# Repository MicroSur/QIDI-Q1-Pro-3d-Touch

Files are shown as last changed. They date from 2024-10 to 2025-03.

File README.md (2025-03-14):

# QIDI-Q1-Pro-3d-Touch

Переделка QIDI Q1 Pro с индуктивного датчика стола на 3д-тач для прошивки OpenQ1

Что плохо:
- все это справедливо для кастомной прошивки OpenQ1 ( https://github.com/frap129/OpenQ1 ), для стоковой прошивки Не подходит.
- нужно отрезать уши крепления у тача.
- подрезать уголок передней крышки головы (фото), чтобы снималась как раньше.
- Переписать в printer.cfg все координаты, где использовался индуктивный датчик на новые (примеры внизу)
- иметь кримпер для фиксации проводов в разъемы
- Это должно напугать и остановить, если нет то дальше...

Что надо:
- 3д-тач. Я брал у треугольников. https://aliexpress.ru/item/32949450525.html?sku_id=12000025395041340
  Можно любой, лишь бы влез в крепление и вы знаете распиновку.
  Распиновка используемого тача по цветам на фото.
- Распечатать крепление (stl), Тач должен крепко садиться в гнездо. У меня из ABS. Ориентацию на столе поменяйте, как вам удобно.
  Крепление в исходнике не мое, отредактировал для QIDI Q1 Pro добавив 10мм проставку. Исходник для qidi max3: https://www.printables.com/model/590047-qidi-x-max-3-x-plus-3-bl-touch-holder
- Распиновка (фото), используются pазъемы на плате головы J7 ( +5, Gnd, IO21 ) и J11 ( IO11 - верхний, второй нижний не использовать ).
  Вторую землю от 3д-тача можно не тащить и никуда не втыкать.

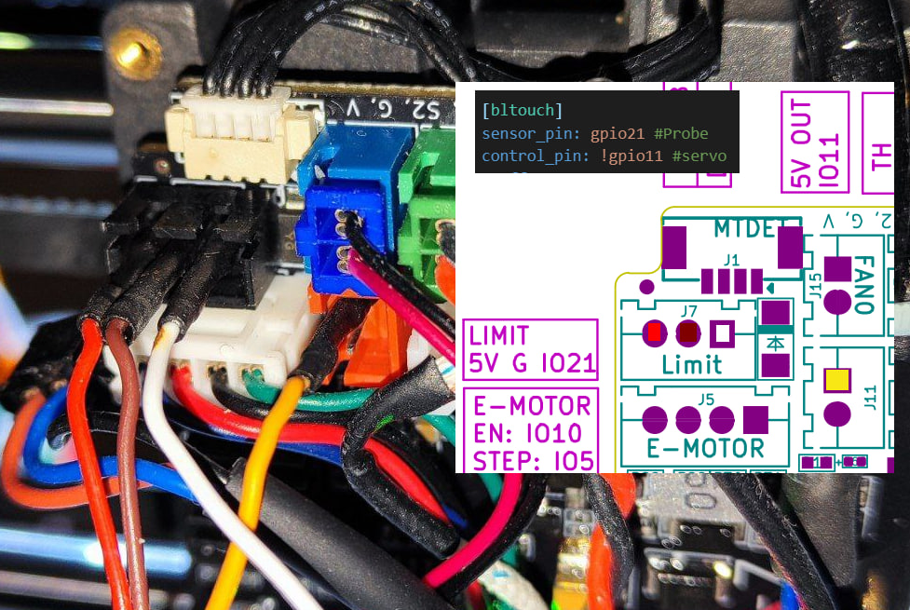
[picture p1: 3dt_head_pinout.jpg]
Распиновка 3д-тач на голове


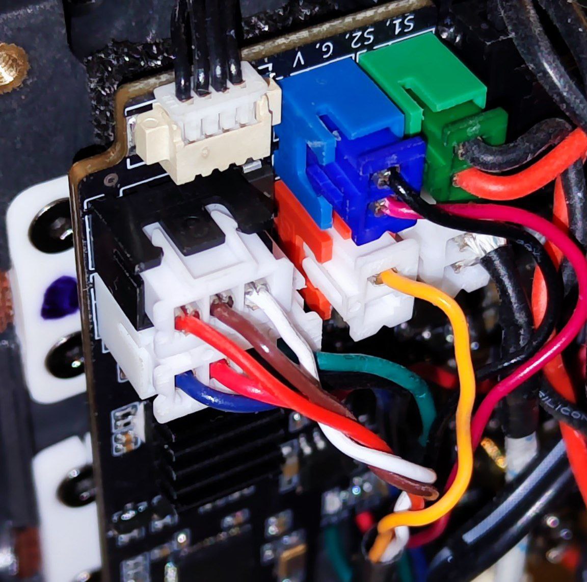
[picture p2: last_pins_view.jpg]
Красивый вариант на голове


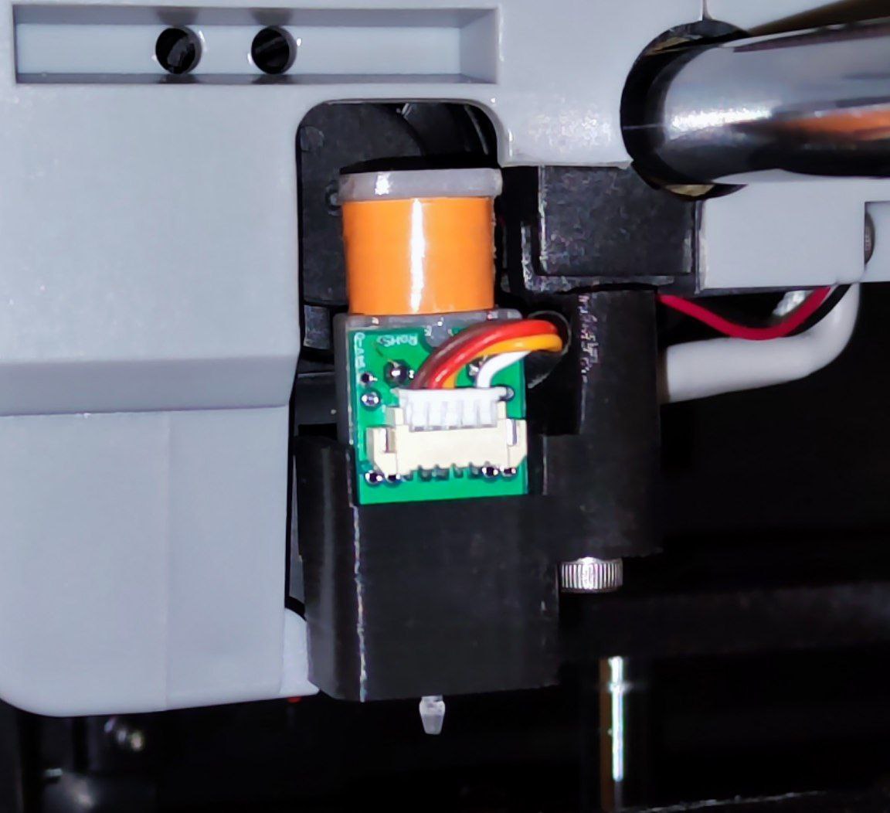
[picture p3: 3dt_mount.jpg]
Крепление


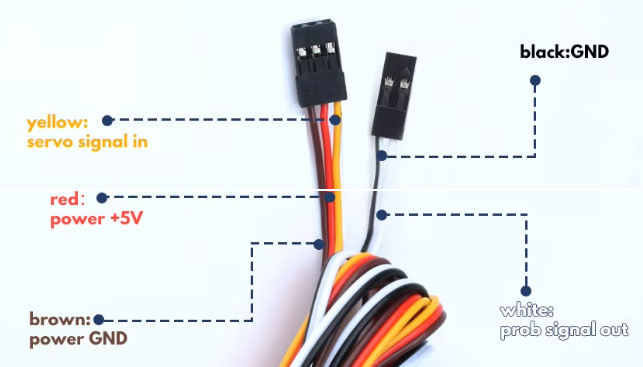
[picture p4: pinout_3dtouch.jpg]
Распиновка 3д-тач по цветам


Пример изменений в printer.cfg

    #Секцию пробы и кулера платы головы закомментировать всю.
    
    #[qdprobe]
    #pin:!gpio21
    #z_offset:0.000001

    # [heater_fan hotend_fan2]
    # pin:gpio11
    # max_power: 1.0
    # shutdown_speed:1.0
    # kick_start_time: 0.5
    # heater: extruder
    # heater_temp: 50.0
    # fan_speed: 1.0
    # off_below: 0

    #добавить секцию bltouch
    [bltouch]
    sensor_pin: gpio21 # Probe
    control_pin: !gpio11 # servo
    x_offset: 29 #induct 17.6 #3d-touch 29
    y_offset: 4.4
    #z_offset: 0.0
    speed: 7.0 
    lift_speed: 20
    samples: 3
    samples_result: median #average
    sample_retract_dist: 2.0
    samples_tolerance: 0.05
    samples_tolerance_retries: 4
    
    [z_tilt]
    z_positions:
        -59,125
        307.5,125
    points:
        0,125
        190,125 #inductive probe = 215,125  # 3d-touch 190,125
    speed: 300
    horizontal_move_z: 5
    retries: 3
    retry_tolerance: 0.01
    
    [bed_mesh]
    speed: 300
    horizontal_move_z: 5 #7 #stock
    mesh_min: 32,15 #20,15 ind
    mesh_max: 230,230 #induct 230,230
    probe_count: 8,8
    algorithm: bicubic
    bicubic_tension: 0.2 #stock
    adaptive_margin: 5
    mesh_pps: 2, 2 #stock
    
    [bed_screws]
    screw1: 10,10
    screw1_name: Front left
    screw2: 190,10 #ind 230,10
    screw2_name: Front right
    screw3: 93,240 #ind 125,240
    screw3_name: Back center
    probe_height: 0.2
    horizontal_move_z: 10
    
    [screws_tilt_adjust]
    screw1: 10,10
    screw1_name: Front left
    screw2: 190,10 #ind 220,10
    screw2_name: Front right
    screw3: 93,230 #ind 125,230
    screw3_name: Back center
    screw_thread: CW-M4

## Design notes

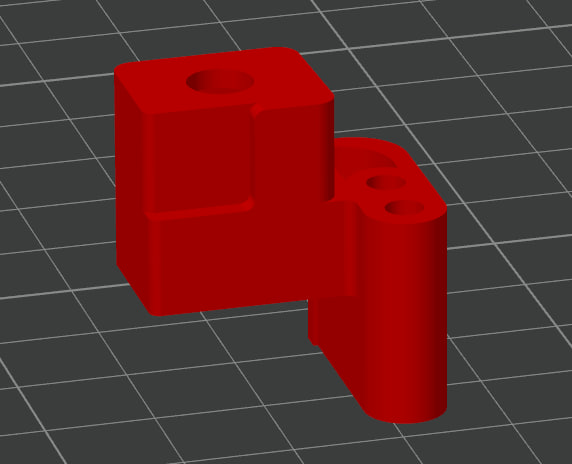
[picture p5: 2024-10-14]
stl.jpg

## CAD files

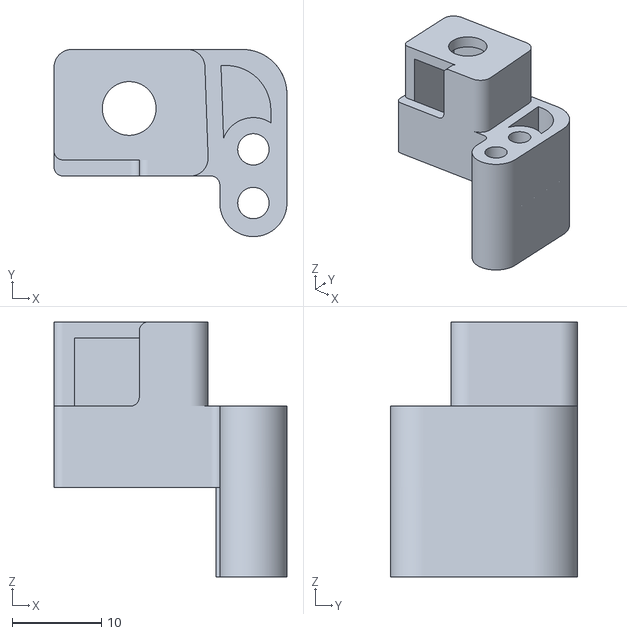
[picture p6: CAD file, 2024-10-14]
blt_qidi_q_1_pro.stl
26.0 x 20.9 x 28.5
